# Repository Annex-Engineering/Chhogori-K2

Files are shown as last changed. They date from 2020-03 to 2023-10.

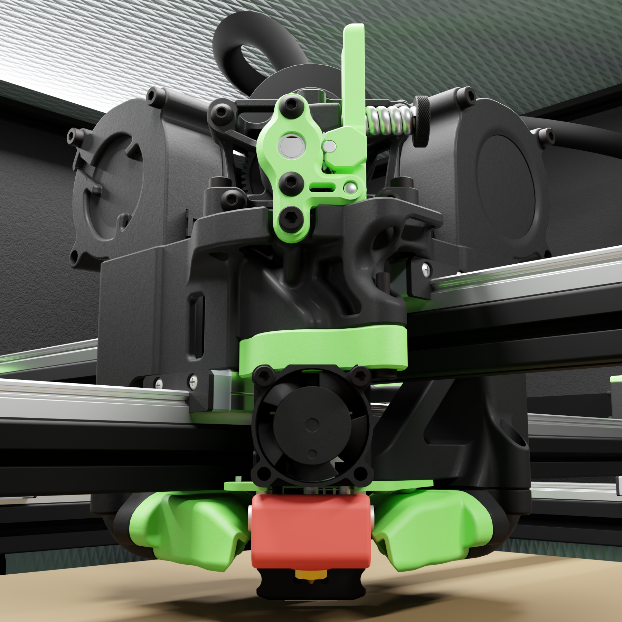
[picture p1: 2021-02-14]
Release_2_2/Images/1800px_k2_r2_render_toolhead_lower.png

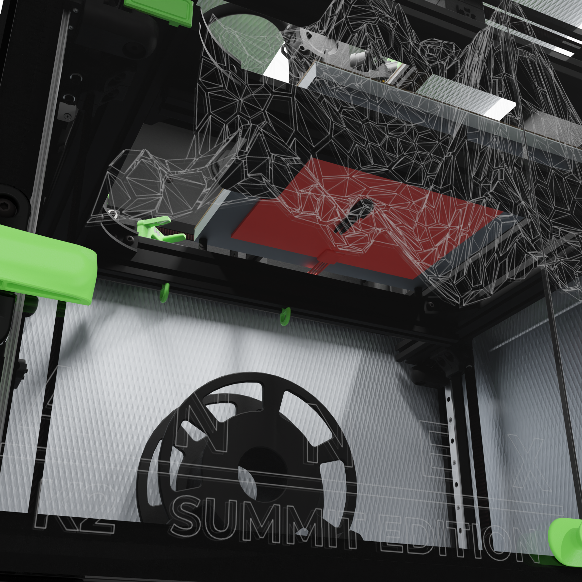
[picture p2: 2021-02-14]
Release_2_2/Images/1800px_k2_r2_render_lowertext.png

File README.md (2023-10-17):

# Chhogori (K2) Printer

## The Current Release is: Release 3 for XY Gantry and Release 2.2 for Z Drive

## Info:
Chhogori (K2): is a Medium Format, Direct Drive, Fully Enclosed FDM Printer.

This is an entirely scratch design, based on the efforts of the "Hypercube Overkill Project" for the XY Motion System, and inspired by all other prior repraps.

Our discord server can be found here: 

Join me on Discord (https://discord.gg/MzTR3zE)

BOM/Sourcing Guide for a 250x250x250 Build can be found here: https://docs.google.com/spreadsheets/d/1O3eyVuQ6M4F03MJSDs4Z71_XyNjXL5HFTZr1jsaAtRc/edit?usp=sharing

Frame Calculator: https://docs.google.com/spreadsheets/d/1hEwPB6xaeSEoHs37LAolL1LlHkrrIWt3NFW9NkrmP7g/edit?usp=sharing

## Stats:
- Fully Enclosed Design
- 2020 and 2040 Frame Members
- Insulated Build Chamber (Not Heated)
- Build Volumes of ~250^3 to 500^3 (use of whole plate available) + additional area to purge and wipe
     - Z can theoretically be 1m tall, just not fully supported or tested

- Direct Drive Extruder (Sherpa Mini or Ascender)

- Shortest Belt Paths Possible, 4 Motors, 2 Per X, 2 Per Y Axis
- Moving Bed, Fixed Gantry

- MGN12H Rails for XY Stationary Rails
- MGN15H Rails for XY Cross (Moving Members)
- MGN12C Rails for Z - using 2.2 parts
- Laser cut metal parts throughout for stiffness and strength (steel recommended in most places, aluminum on moving components)
- 12mm 2GT Belts on XY Motion 
- 12mm 2GT Belts with 20:1 Worm Drive on Z to lift the Bed 
	 - Hybrid Laser Cut Metal and Printed Part Construction
	 - Legacy Support for 15mm 3HTD belts also offered
- Heavy Duty Bearings
- NEMA17 Motors XYZ

- Minimal Printed Parts (ASA Required, PC Recommended for motion components)

- Fysetc Spider or S6 Controller + BTT Expander Board with Klipper Required
- Mosquito Style, Dragon Style, Mosquito Magnum+, Nitram's VolcoMosquito, and many other hotends supported
- 24V Power Standard, 48V Optional and Preferred
- Mains Bed

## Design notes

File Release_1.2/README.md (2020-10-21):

# Chhogori (K2) Printer - Summit Edition

These parts are purely pre-release at this point, please use with caution.

Use tab 2 on the frame calculator if you would like to build to this revision, please use discord for support

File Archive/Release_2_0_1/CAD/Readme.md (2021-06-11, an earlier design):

#CAD

Files are released in parasolid format only and will not be shared in any other format. (We have quality standards, STEP and IGES enjoy spitting out corrupted files, sorry)

By using these cad files, you agree to share any and all mods, that you develop, under the "ANNEX License", which can be found under the main level of this repo.

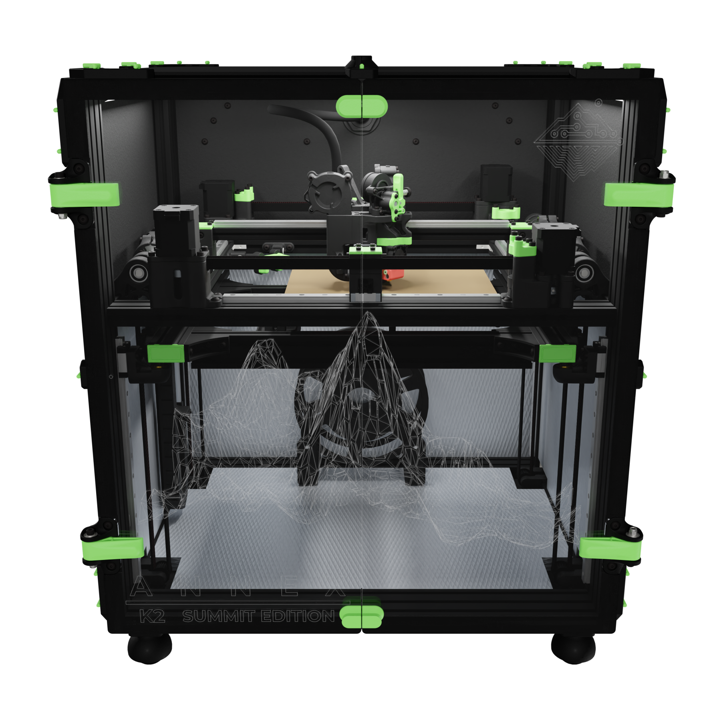
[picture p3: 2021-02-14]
Release_2_2/Images/1800px_k2_r2_render_center.png

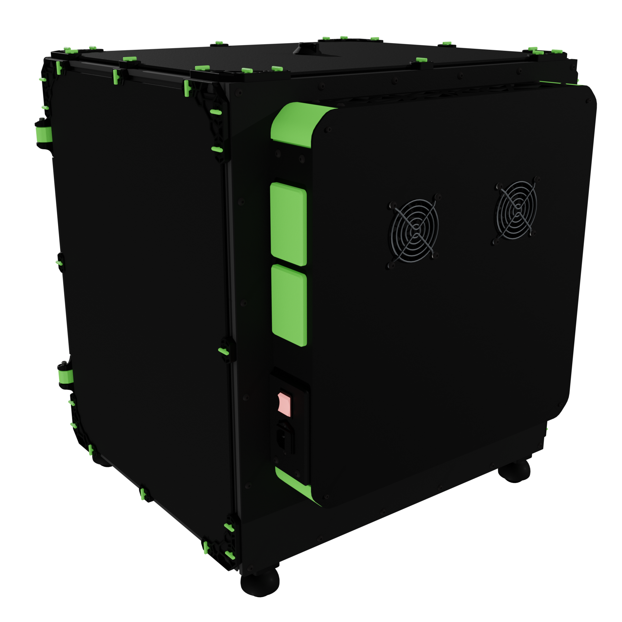
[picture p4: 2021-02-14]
Release_2_2/Images/1800px_k2_r2_render_rear.png

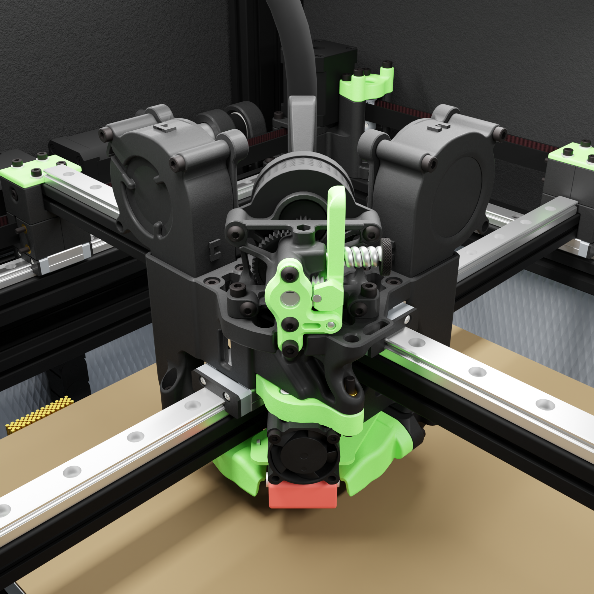
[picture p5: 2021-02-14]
Release_2_2/Images/1800px_k2_r2_render_toolhead_upper.png

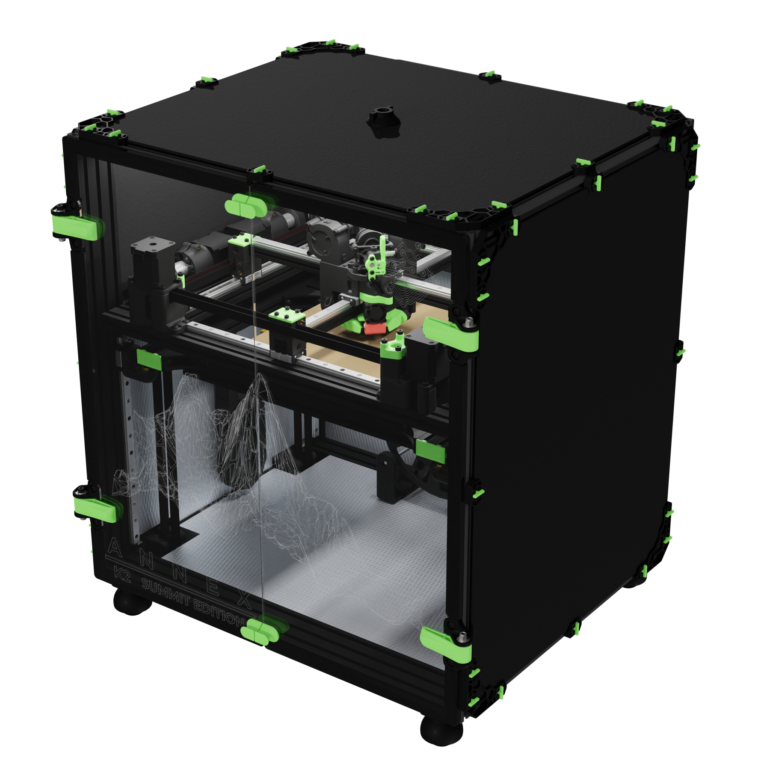
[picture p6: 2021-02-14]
Release_2_2/Images/1800px_k2_r2_render_dimetric.png

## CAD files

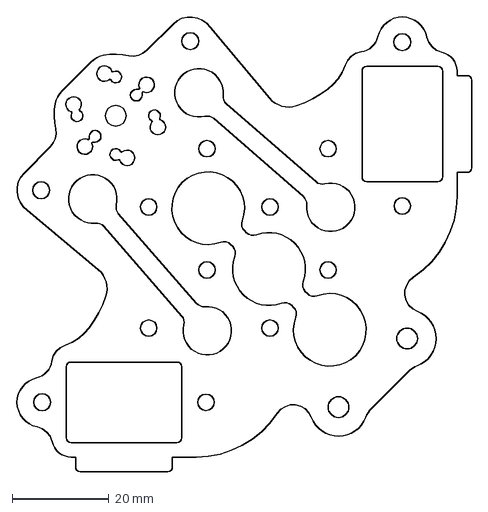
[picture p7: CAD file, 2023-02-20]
Release_3_0/DXFs/Toolhead/toolhead_main_plate_sherpa_mini_x2_rev4_2mm_aluminum.DXF
93.9 x 93.9 mm

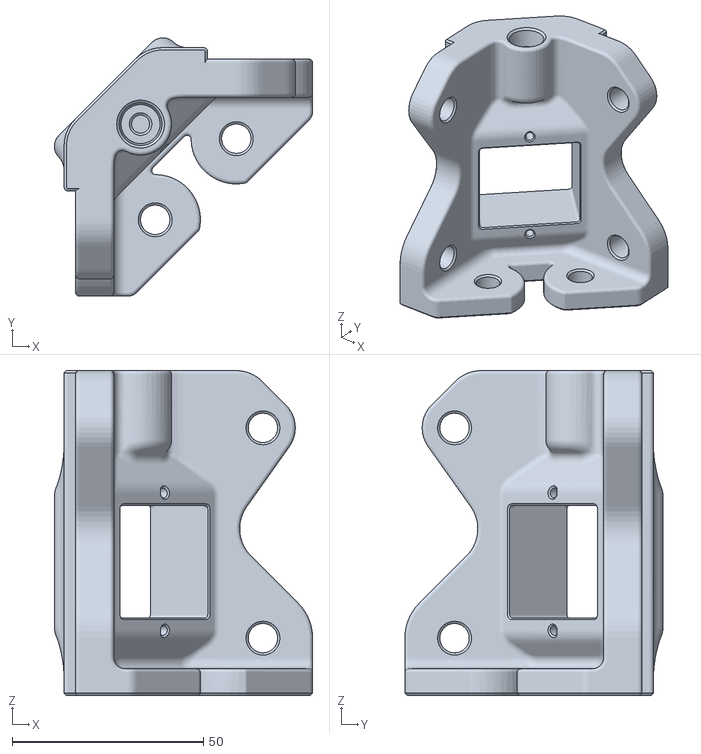
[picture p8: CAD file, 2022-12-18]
Release_3_0/STLs/Electronics_Box/electronics_box_corner_mains_inlet_x1_rev4.STL
67.6 x 67.6 x 85.0

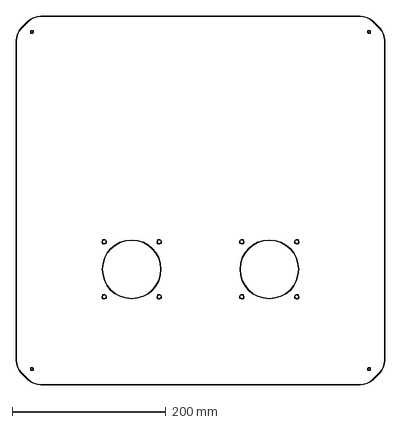
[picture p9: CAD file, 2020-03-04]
DXFs/Electronics_Box/electronics_box_cover_x1_rev1.DXF
479.0 x 479.0 mm

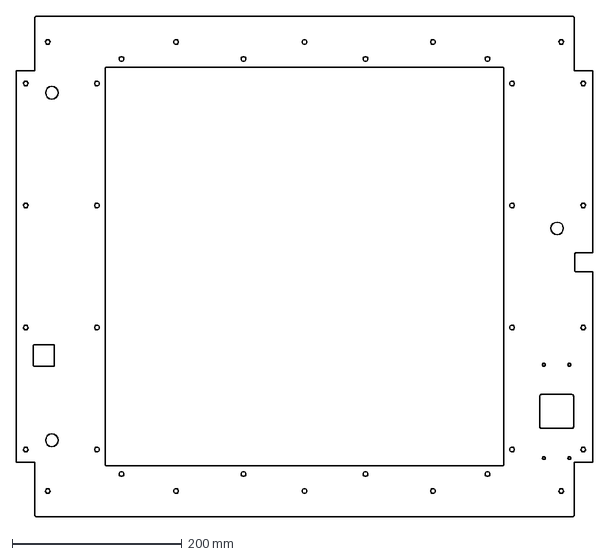
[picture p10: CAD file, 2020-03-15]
DXFs/Panels/Gantry_Deck_Panel_350mm_x_350mm_Rev3.DXF
680.0 x 590.0 mm

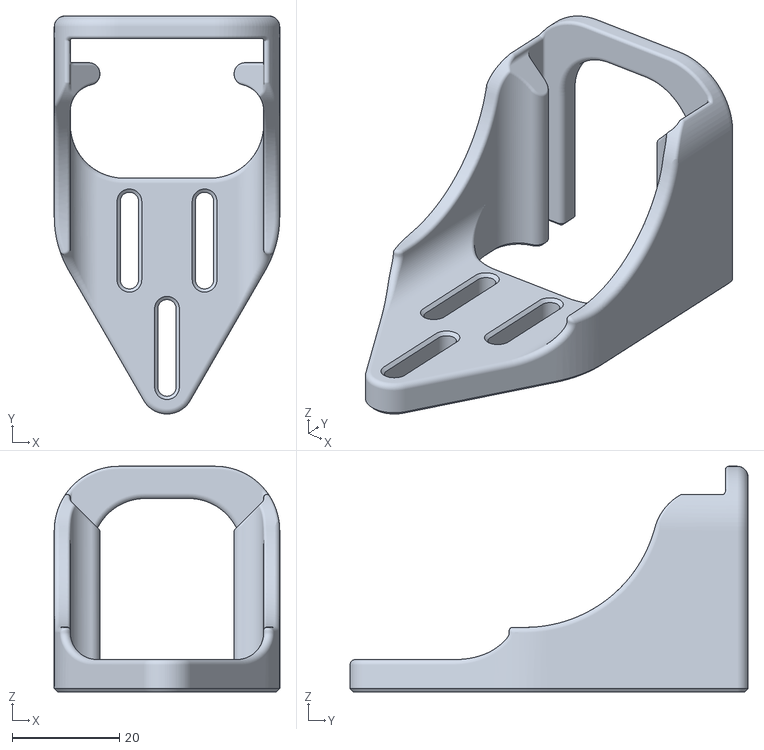
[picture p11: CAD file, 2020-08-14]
Release_1.2/STLs/Mesh_Bed_Probe/Magnetic_Probe/magnetic_probe_dock_x1_rev5.STL
42.0 x 74.1 x 42.0

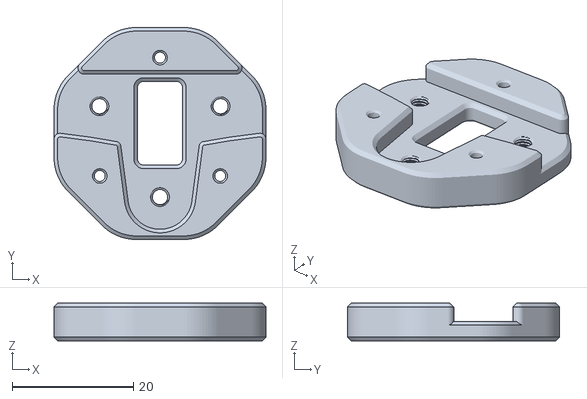
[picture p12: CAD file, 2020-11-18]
Release_1.2/STLs/Mesh_Bed_Probe/Piton_Probe/[a]_piton_probe_plate_6x3_x1_rev2.STL
35.0 x 35.0 x 6.20

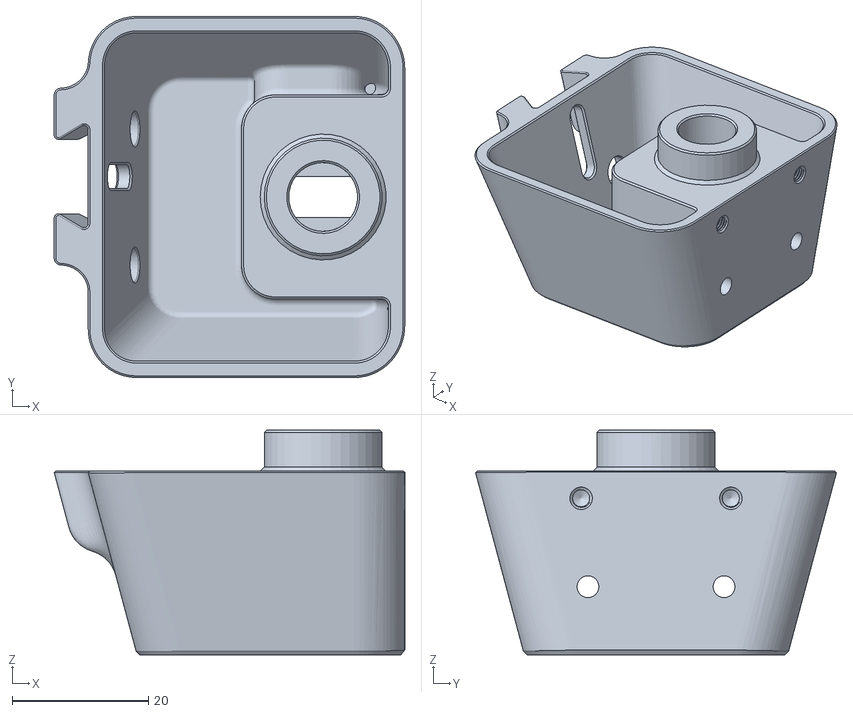
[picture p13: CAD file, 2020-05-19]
Release_1.2/STLs/Misc/z_endstop_housing_x1_rev1.STL
51.5 x 53.1 x 33.0

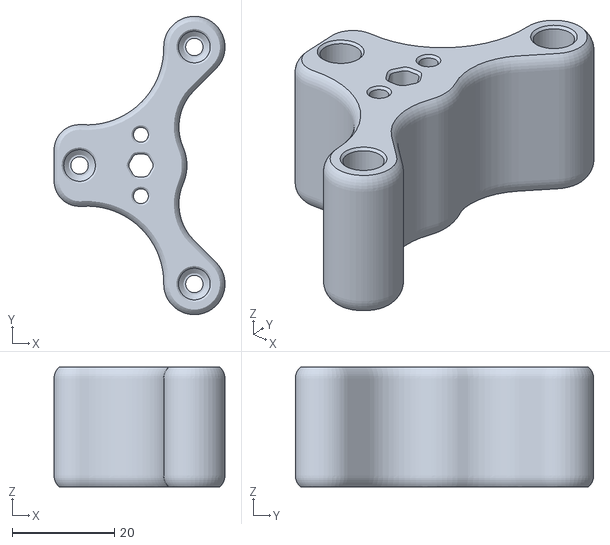
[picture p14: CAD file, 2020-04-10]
Release_1.2/STLs/XY_Carriage/Tool_Mounts/xy_carriage_mosquito_tool_mount_x1_rev3.STL
33.4 x 58.3 x 23.4

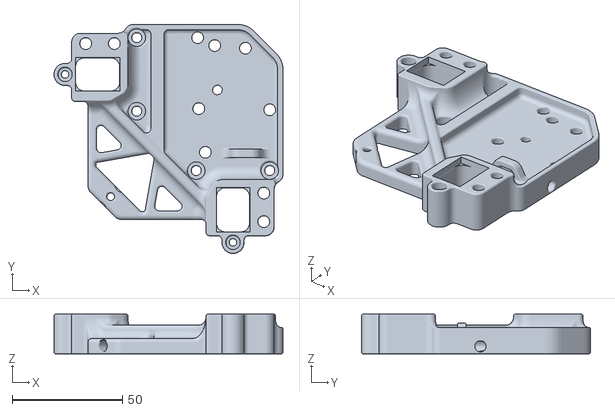
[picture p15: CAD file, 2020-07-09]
Release_1.2/STLs/XY_Carriage/Top_Plates/sherpa_tall_xy_carriage_top_plate_x1_rev1.STL
104.0 x 104.0 x 18.0

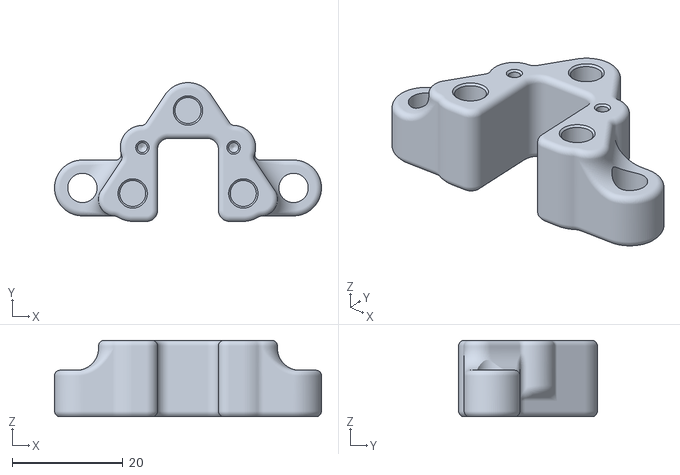
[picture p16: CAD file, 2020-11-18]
Release_1.2/STLs/XY_Carriage/xy_carriage_piton_probe_holder_mosquito_x1_rev3.STL
48.3 x 25.1 x 13.8

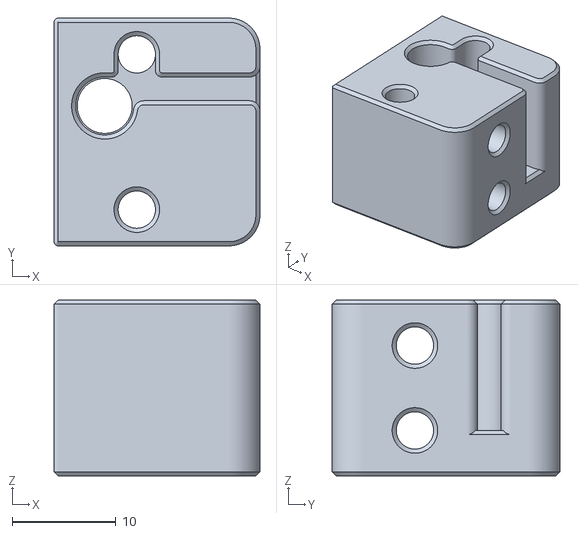
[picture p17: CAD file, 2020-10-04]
Release_1.2/STLs/XY_Gantry/xy_tensioner_left_20t_drive_x4_rev3.STL
19.9 x 22.0 x 17.0

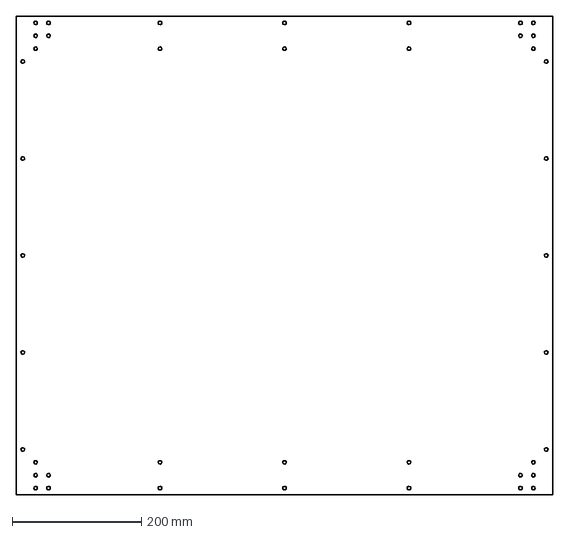
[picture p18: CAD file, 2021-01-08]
Release_2/DXFs/Optional_Laser_Cut_Panels/Bottom_500mm_x_500mm_Rev1.DXF
830.0 x 740.0 mm

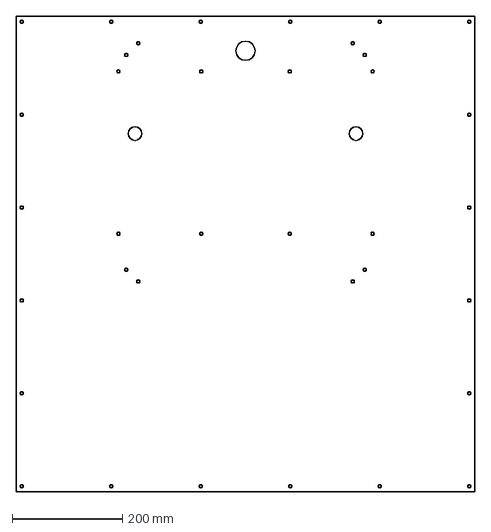
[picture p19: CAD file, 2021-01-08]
Release_2/DXFs/Panels/Back_Panel_500mm_x_500mm_Rev1.DXF
830.0 x 861.0 mm

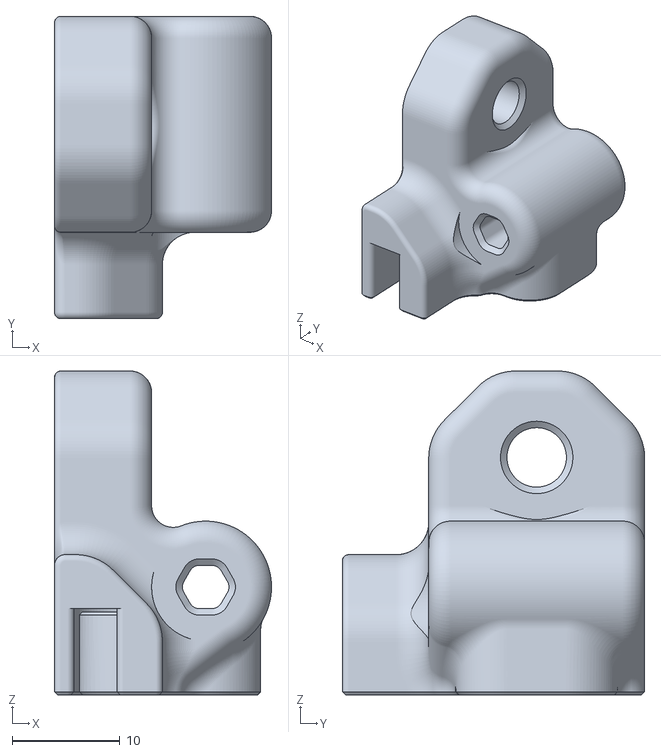
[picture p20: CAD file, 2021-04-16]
Release_2/STLs/Belted_Z_Drive/[a]_belted_z_tensioner_b1_x4_rev4.STL
20.1 x 28.0 x 30.0

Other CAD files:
Release_2/STLs/Electronics_Brackets/bigtreetech_skr_mounting_bracket_x2_rev4.STL
Release_2_1/DXFs/12mm_2GT_Belted_Z_Drive/3mm_stainless_belted_worm_z_metal_top_40+20to1_x4_rev1.DXF
Release_2_1/DXFs/15mm_3HTD_Belted_Z_Drive/3mm_stainless_belted_worm_z_metal_top_60to1_x4_rev2.DXF
Release_2_1/DXFs/Electronics_Box/electronics_box_side_panel_power_inet_x1_rev1.DXF
Archive/Release_1.2/CAD/BASS_Fan_Ducts.x_t
Archive/Release_1.2/CAD/FYSETC_S6_Mounting_Frame.x_t
Archive/Release_1.2/CAD/Front Door_Rev1.2-12-08-2020.x_t
Archive/Release_1.2/CAD/Piton_Probe_Assembly_11-18-2020.x_t
Archive/Release_1.2/DXFs/Electronics_Box/electronics_box_side_panel_TE_power_inlet_x1_rev2.DXF
Archive/Release_1.2/DXFs/Optional_Laser_Cut_Panels/Bottom_200mm_x_200mm_Rev1.DXF
Archive/Release_1.2/DXFs/Optional_Laser_Cut_Panels/Bottom_250mm_x_250mm_Rev1.DXF
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

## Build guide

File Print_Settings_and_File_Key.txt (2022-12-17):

Primary Color: nothing at start of file name
Accent Color: [a]_ at start of file name
Quantity Required: _x# near end of file name
File Revision: _Rev# at end of file name

Nozzle Size: 0.5mm 
Recommended FDM Materials: ASA, Polymaker or 3DXTech Recommended
Alternate Approved FDM Materials: PC, 3DXTech Recommended
Layer Height: 0.25mm
Extrusion Width: Forced 0.5mm
Infill Percentage: 40% minimum (at 0.8mm Width)
Infill Type: Grid, Gyroid, Honeycomb, Triangle or Cubic
Wall Count: 3 minimum (at 0.5mm Width)
Solid Top/Bottom Layers: 4 minimum (at 0.5mm Height)

Nozzle Size: 0.4mm 
Recommended FDM Materials: ASA, Polymaker or 3DXTech Recommended
Alternate Approved FDM Materials: PC, 3DXTech Recommended
Layer Height: 0.20mm or 0.25mm
Extrusion Width: Forced 0.4mm
Infill Percentage: 40% minimum (at 0.6mm Width)
Infill Type: Grid, Gyroid, Honeycomb, Triangle or Cubic
Wall Count: 4 minimum (at 0.4mm Width)
Solid Top/Bottom Layers: 4 minimum (at 0.25mm Height)

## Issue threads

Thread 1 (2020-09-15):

I don't understand what the endstop in this place does

du5778, 2020-09-15:
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

Tuz550, 2020-09-15:
The printer has a vertically moving bed, printing at the top and moving downwards. From the picture, it looks like that is the lowest extent of the Z axis.

Annex-Engineering, 2020-09-15:
Those switches are emergency stop buttons, because the bed is on springs, if one was to ram the nozzle into the bed by accident, this will turn the machine off. They are entirely optional.

Closed 2020-09-15.

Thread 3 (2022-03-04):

Assembly issues: 20:1 12mm worm Z drive

ameyp, 2022-03-04:
List of issues I encountered during assembly:

1. The long bolts holding the motor should be m3x45 instead of m3x40. The distance between the top and bottom of the drive is 39mm, leaving just 1mm on a 40mm bolt.
2. Some Aliexpress spur have 7mm hubs instead of 6mm, making it necessary to use multiple 1mm shims instead of 3mm spacers in order to get full tooth engagement between the worm and the spur

Closed 2024-04-24.

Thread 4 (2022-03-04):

Assembly issues: Z tensioner

ameyp, 2022-03-04:
List of issues I encountered during assembly:

- The two spacers that go on the shoulder bolt are swapped. The M5 one needs to be on the threaded side and the M6 one needs to be on the head side.

Closed 2024-04-24.

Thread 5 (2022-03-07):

Back right X stepper collides with right cable pass-through on the 2.2 frame setup

wlhlm, 2022-03-07:
Seems like back right stepper on the gantry obstructs the cable hole on the new 2040 frame:
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

Trails5000, 2022-03-07:
fixed with commit: https://github.com/Annex-Engineering/Chhogori-K2/commit/2baa07d4b91d5fae562b1b8711de88642b03c4b1

Closed 2022-03-07.

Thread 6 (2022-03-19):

Assembly issues: Z idler

ameyp, 2022-03-19:
List of issues I encountered during assembly:

- Tensioning the Z makes the rotation on which Z idlers are mounted rotate. The only ways to prevent this at present are by using external brackets or a bolted bottom panel

Closed 2024-04-24.

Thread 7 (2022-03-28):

Assembly issues: Backpack

ameyp, 2022-03-28:
List of issues I encountered during assembly

- The backpack extrusions should be mounted using M5x8 BHCS, the eDrawing says M5x10 BHCS. The latter are too long and bottom out with a 1mm gap left between the bolt head and the back panel
- The BOM needs a lot more M5x8 BHCS. Right now it says 2, but everything in the backpack uses them

Closed 2024-04-24.

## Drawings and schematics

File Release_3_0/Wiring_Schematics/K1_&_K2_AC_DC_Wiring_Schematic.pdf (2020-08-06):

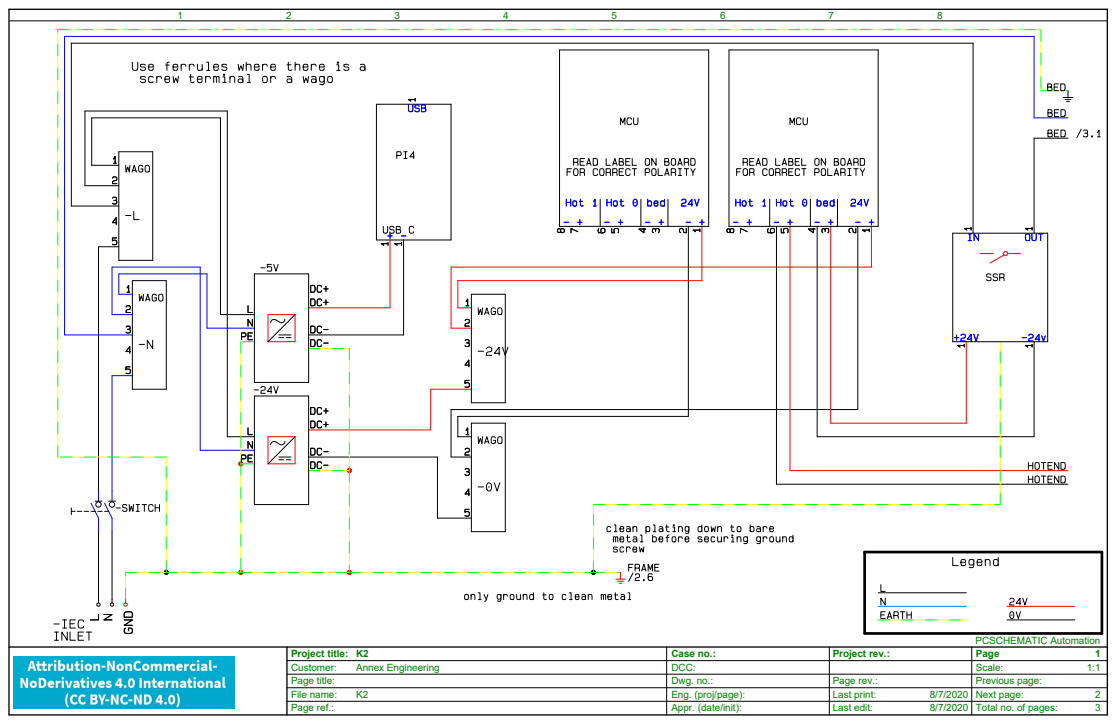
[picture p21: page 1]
PCSCHEMATIC Automation

Project title: K2 | Case no.: | Project rev.: | Page 1
Customer: Annex Engineering | DCC: | | Scale: 1:1
Page title: | Dwg. no.: | Page rev.: | Previous page:
File name: K2 | Eng. (proj/page): | Last print: 8/7/2020 | Next page: 2
Page ref.: | Appr. (date/init): | Last edit: 8/7/2020 | Total no. of pages: 3

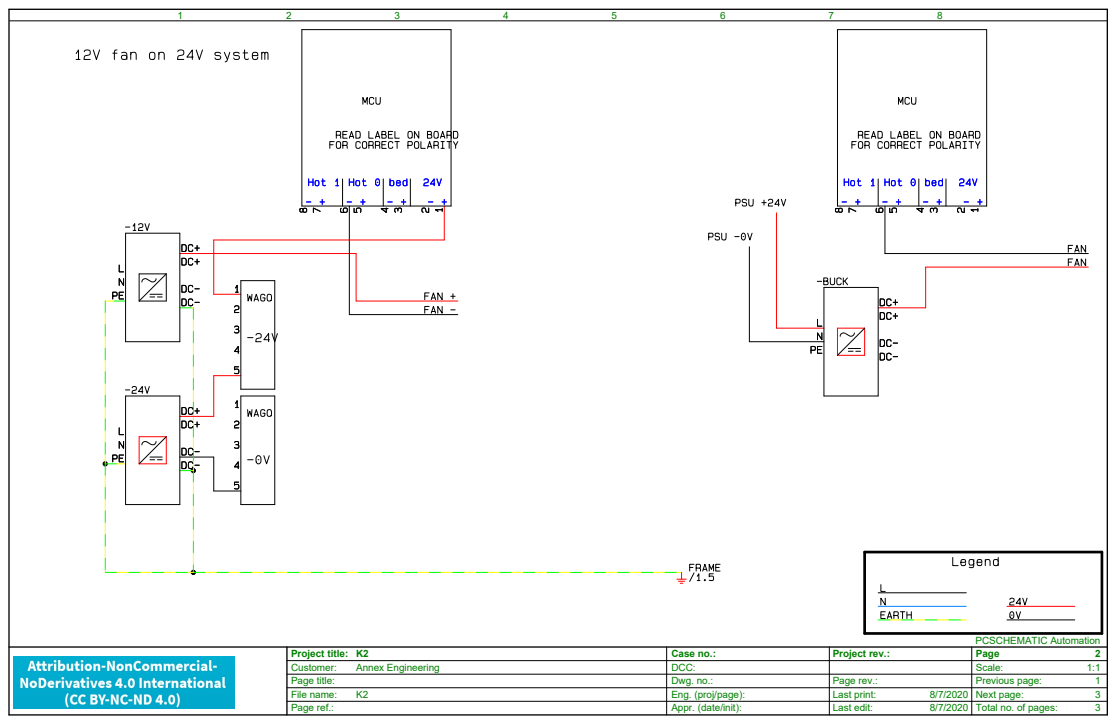
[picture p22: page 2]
PCSCHEMATIC Automation

Project title: K2 | Case no.: | Project rev.: | Page 2
Customer: Annex Engineering | DCC: | | Scale: 1:1

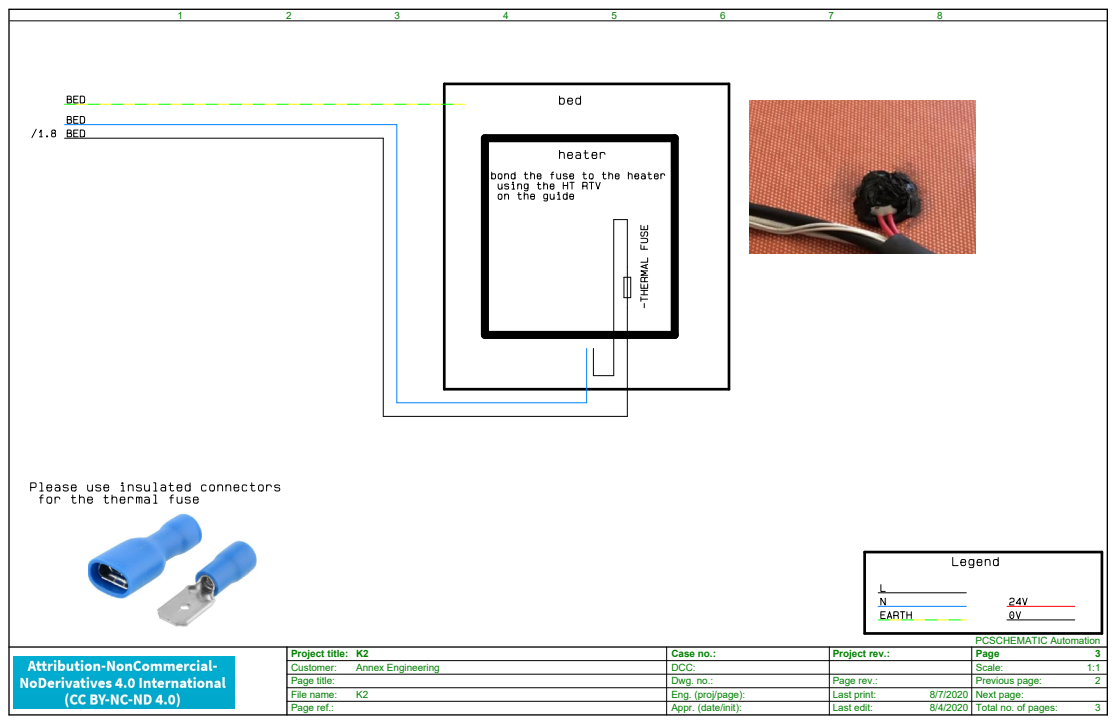
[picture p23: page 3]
PCSCHEMATIC Automation

Project title: K2 | Case no.: | Project rev.: | Page 3
Customer: Annex Engineering | DCC: | | Scale: 1:1

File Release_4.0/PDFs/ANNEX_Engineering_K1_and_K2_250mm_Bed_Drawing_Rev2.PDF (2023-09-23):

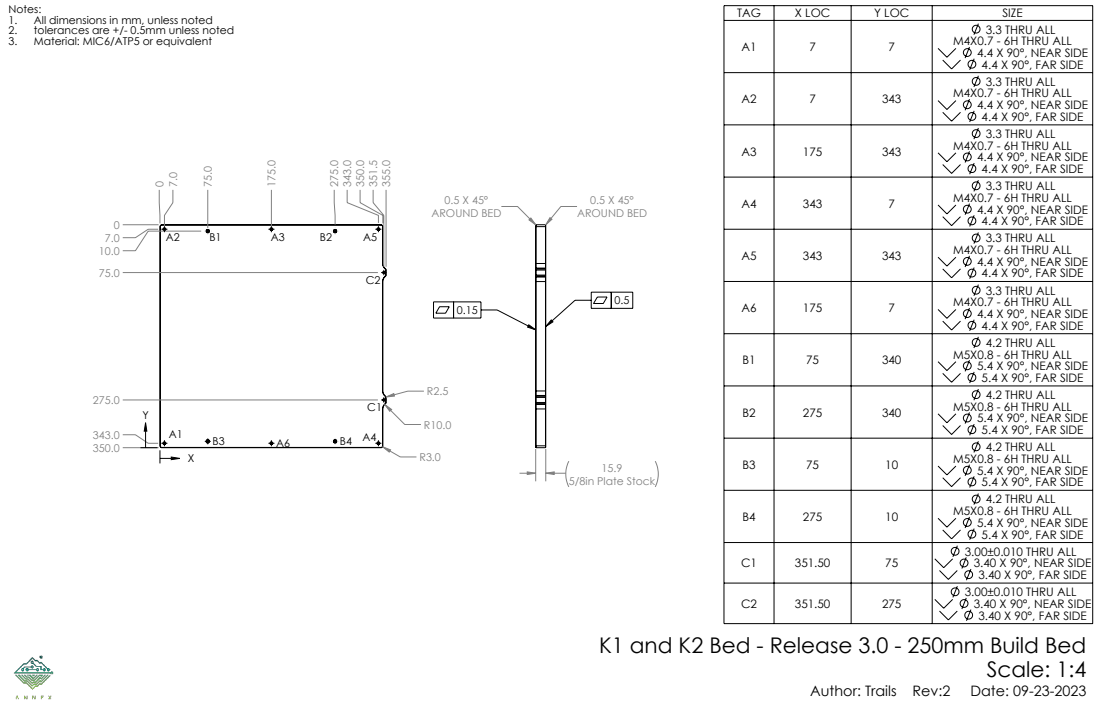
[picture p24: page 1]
5/8in Plate Stock; 0.5 X 45° AROUND BED; Scale: 1:4

Notes:
1. All dimensions in mm, unless noted
2. tolerances are +/- 0.5mm unless noted
3. Material: MIC6/ATP5 or equivalent

TAG | X LOC | Y LOC | SIZE
A1 | 7 | 7 | 3.3 THRU ALL M4X0.7 - 6H THRU ALL 4.4 X 90°, NEAR SIDE 4.4 X 90°, FAR SIDE

A2 | 7 | 343 | 3.3 THRU ALL M4X0.7 - 6H THRU ALL 4.4 X 90°, NEAR SIDE 4.4 X 90°, FAR SIDE

A3 | 175 | 343 | 3.3 THRU ALL M4X0.7 - 6H THRU ALL 4.4 X 90°, NEAR SIDE 4.4 X 90°, FAR SIDE

A4 | 343 | 7 | 3.3 THRU ALL M4X0.7 - 6H THRU ALL 4.4 X 90°, NEAR SIDE 4.4 X 90°, FAR SIDE

A5 | 343 | 343 | 3.3 THRU ALL M4X0.7 - 6H THRU ALL 4.4 X 90°, NEAR SIDE 4.4 X 90°, FAR SIDE

A6 | 175 | 7 | 3.3 THRU ALL M4X0.7 - 6H THRU ALL 4.4 X 90°, NEAR SIDE 4.4 X 90°, FAR SIDE

B1 | 75 | 340 | 4.2 THRU ALL M5X0.8 - 6H THRU ALL 5.4 X 90°, NEAR SIDE 5.4 X 90°, FAR SIDE

B2 | 275 | 340 | 4.2 THRU ALL M5X0.8 - 6H THRU ALL 5.4 X 90°, NEAR SIDE 5.4 X 90°, FAR SIDE

B3 | 75 | 10 | 4.2 THRU ALL M5X0.8 - 6H THRU ALL 5.4 X 90°, NEAR SIDE 5.4 X 90°, FAR SIDE

B4 | 275 | 10 | 4.2 THRU ALL M5X0.8 - 6H THRU ALL 5.4 X 90°, NEAR SIDE 5.4 X 90°, FAR SIDE

C1 | 351.50 | 75 | 3.00±0.010 THRU ALL 3.40 X 90°, NEAR SIDE 3.40 X 90°, FAR SIDE

C2 | 351.50 | 275 | 3.00±0.010 THRU ALL 3.40 X 90°, NEAR SIDE 3.40 X 90°, FAR SIDE

K1 and K2 Bed - Release 3.0 - 250mm Build Bed

Author: Trails Rev:2 Date: 09-23-2023

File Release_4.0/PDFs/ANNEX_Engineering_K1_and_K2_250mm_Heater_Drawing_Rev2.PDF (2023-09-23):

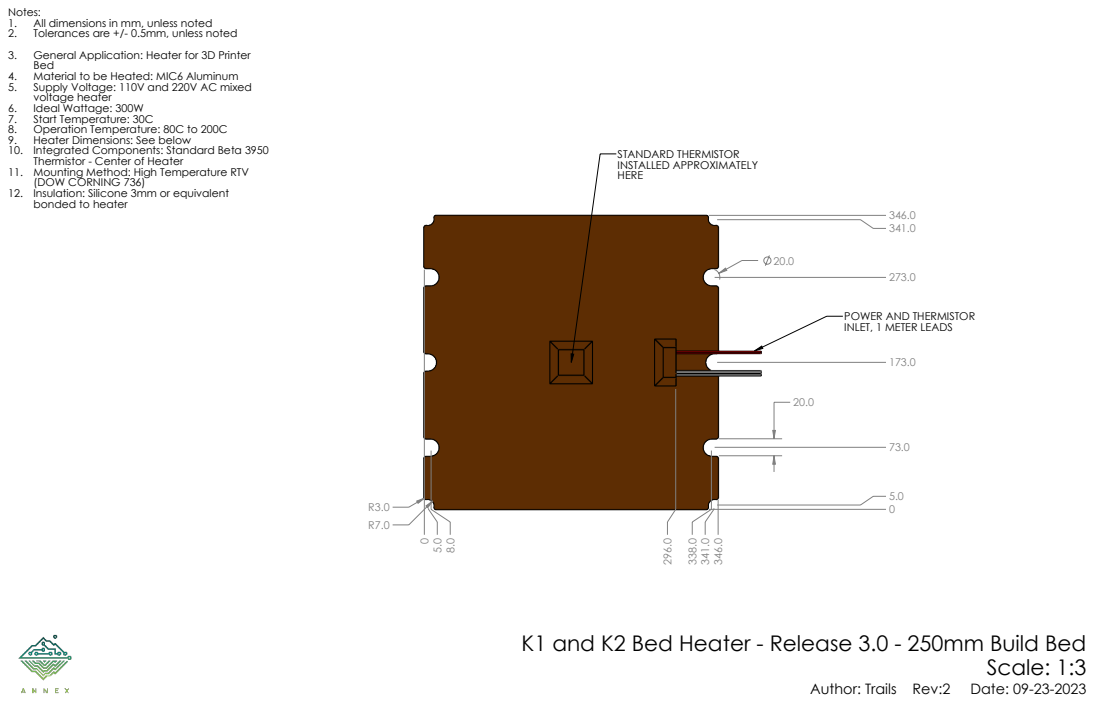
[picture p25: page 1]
STANDARD THERMISTOR INSTALLED APPROXIMATELY; Scale: 1:3

Notes:
1. All dimensions in mm, unless noted
2. Tolerances are +/- 0.5mm, unless noted
3. General Application: Heater for 3D Printer
Bed
4. Material to be Heated: MIC6 Aluminum
5. Supply Voltage: 110V and 220V AC mixed
voltage heater
6. Ideal Wattage: 300W
7. Start Temperature: 30C
8. Operation Temperature: 80C to 200C
9. Heater Dimensions: See below
10. Integrated Components: Standard Beta 3950
Thermistor - Center of Heater
11. Mounting Method: High Temperature RTV
(DOW CORNING 736)
12. Insulation: Silicone 3mm or equivalent
bonded to heater

POWER AND THERMISTOR
INLET, 1 METER LEADS

K1 and K2 Bed Heater - Release 3.0 - 250mm Build Bed

Author: Trails Rev:2 Date: 09-23-2023

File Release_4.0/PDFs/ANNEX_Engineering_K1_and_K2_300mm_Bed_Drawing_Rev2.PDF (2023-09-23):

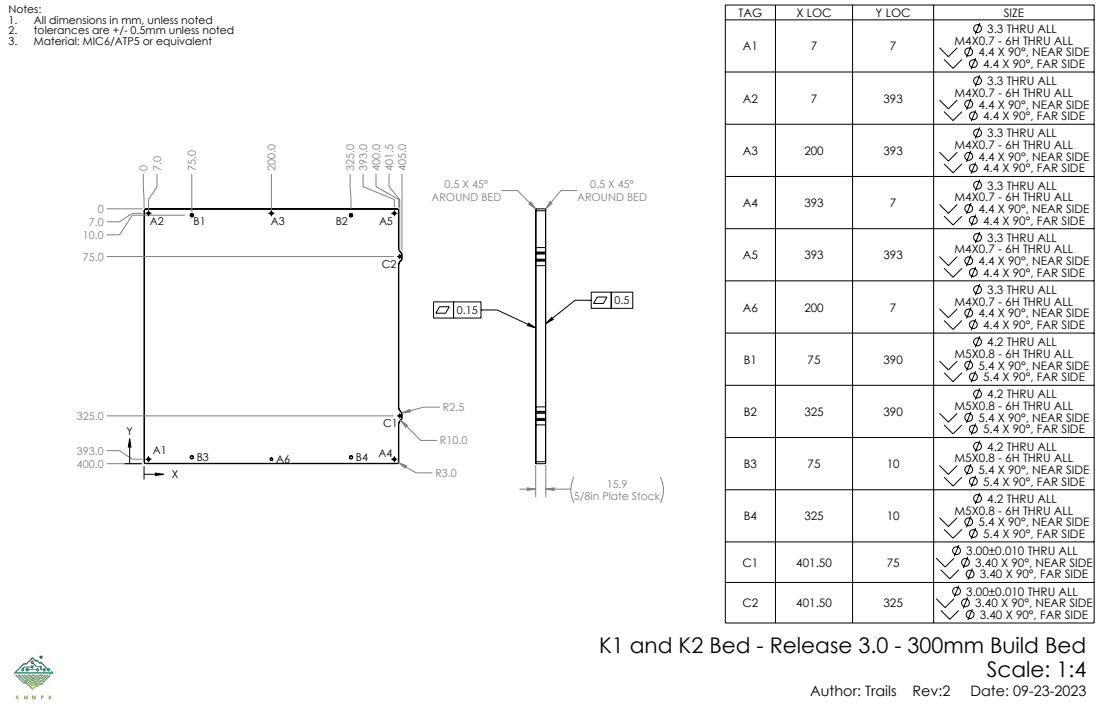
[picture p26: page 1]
5/8in Plate Stock; 0.5 X 45° AROUND BED; Scale: 1:4

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

A2 | 7 | 393 | 3.3 THRU ALL M4X0.7 - 6H THRU ALL 4.4 X 90°, NEAR SIDE 4.4 X 90°, FAR SIDE

A3 | 200 | 393 | 3.3 THRU ALL M4X0.7 - 6H THRU ALL 4.4 X 90°, NEAR SIDE 4.4 X 90°, FAR SIDE

A4 | 393 | 7 | 3.3 THRU ALL M4X0.7 - 6H THRU ALL 4.4 X 90°, NEAR SIDE 4.4 X 90°, FAR SIDE

A5 | 393 | 393 | 3.3 THRU ALL M4X0.7 - 6H THRU ALL 4.4 X 90°, NEAR SIDE 4.4 X 90°, FAR SIDE

A6 | 200 | 7 | 3.3 THRU ALL M4X0.7 - 6H THRU ALL 4.4 X 90°, NEAR SIDE 4.4 X 90°, FAR SIDE

B1 | 75 | 390 | 4.2 THRU ALL M5X0.8 - 6H THRU ALL 5.4 X 90°, NEAR SIDE 5.4 X 90°, FAR SIDE

B2 | 325 | 390 | 4.2 THRU ALL M5X0.8 - 6H THRU ALL 5.4 X 90°, NEAR SIDE 5.4 X 90°, FAR SIDE

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

B4 | 325 | 10 | 4.2 THRU ALL M5X0.8 - 6H THRU ALL 5.4 X 90°, NEAR SIDE 5.4 X 90°, FAR SIDE

C1 | 401.50 | 75 | 3.00±0.010 THRU ALL 3.40 X 90°, NEAR SIDE 3.40 X 90°, FAR SIDE

C2 | 401.50 | 325 | 3.00±0.010 THRU ALL 3.40 X 90°, NEAR SIDE 3.40 X 90°, FAR SIDE

K1 and K2 Bed - Release 3.0 - 300mm Build Bed

Author: Trails Rev:2 Date: 09-23-2023

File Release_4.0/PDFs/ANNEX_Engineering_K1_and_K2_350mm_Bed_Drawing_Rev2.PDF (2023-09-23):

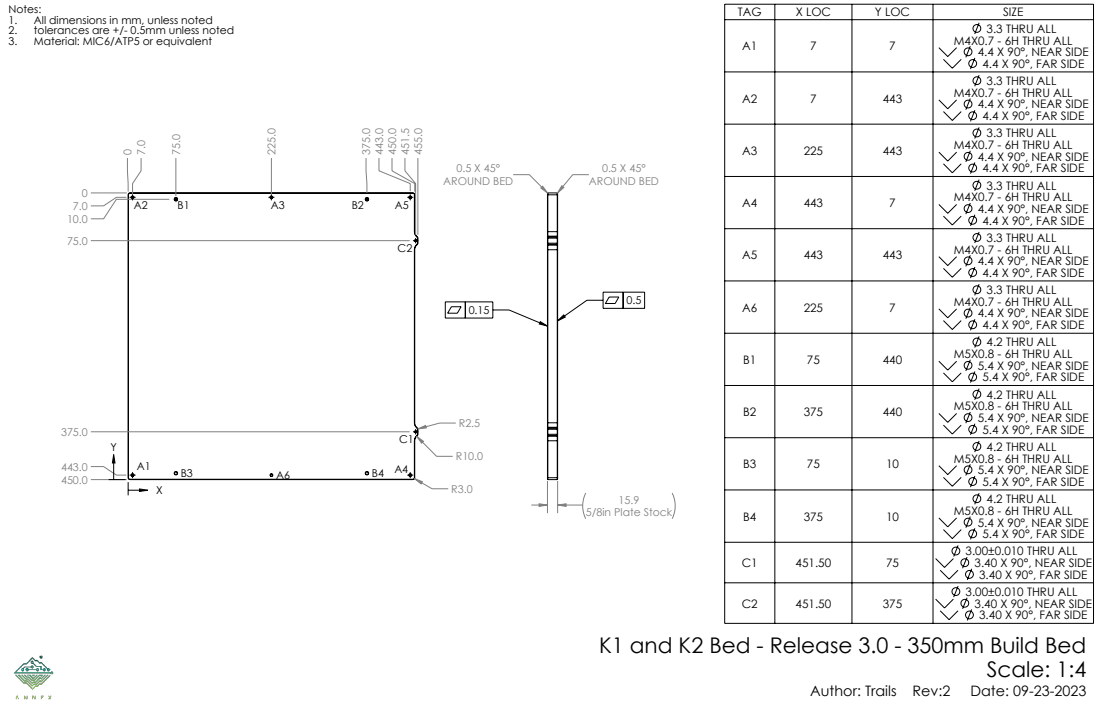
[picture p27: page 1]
5/8in Plate Stock; 0.5 X 45° AROUND BED; Scale: 1:4

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

A2 | 7 | 443 | 3.3 THRU ALL M4X0.7 - 6H THRU ALL 4.4 X 90°, NEAR SIDE 4.4 X 90°, FAR SIDE

A3 | 225 | 443 | 3.3 THRU ALL M4X0.7 - 6H THRU ALL 4.4 X 90°, NEAR SIDE 4.4 X 90°, FAR SIDE

A4 | 443 | 7 | 3.3 THRU ALL M4X0.7 - 6H THRU ALL 4.4 X 90°, NEAR SIDE 4.4 X 90°, FAR SIDE

A5 | 443 | 443 | 3.3 THRU ALL M4X0.7 - 6H THRU ALL 4.4 X 90°, NEAR SIDE 4.4 X 90°, FAR SIDE

A6 | 225 | 7 | 3.3 THRU ALL M4X0.7 - 6H THRU ALL 4.4 X 90°, NEAR SIDE 4.4 X 90°, FAR SIDE

B1 | 75 | 440 | 4.2 THRU ALL M5X0.8 - 6H THRU ALL 5.4 X 90°, NEAR SIDE 5.4 X 90°, FAR SIDE

B2 | 375 | 440 | 4.2 THRU ALL M5X0.8 - 6H THRU ALL 5.4 X 90°, NEAR SIDE 5.4 X 90°, FAR SIDE

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

B4 | 375 | 10 | 4.2 THRU ALL M5X0.8 - 6H THRU ALL 5.4 X 90°, NEAR SIDE 5.4 X 90°, FAR SIDE

C1 | 451.50 | 75 | 3.00±0.010 THRU ALL 3.40 X 90°, NEAR SIDE 3.40 X 90°, FAR SIDE

C2 | 451.50 | 375 | 3.00±0.010 THRU ALL 3.40 X 90°, NEAR SIDE 3.40 X 90°, FAR SIDE

K1 and K2 Bed - Release 3.0 - 350mm Build Bed

Author: Trails Rev:2 Date: 09-23-2023

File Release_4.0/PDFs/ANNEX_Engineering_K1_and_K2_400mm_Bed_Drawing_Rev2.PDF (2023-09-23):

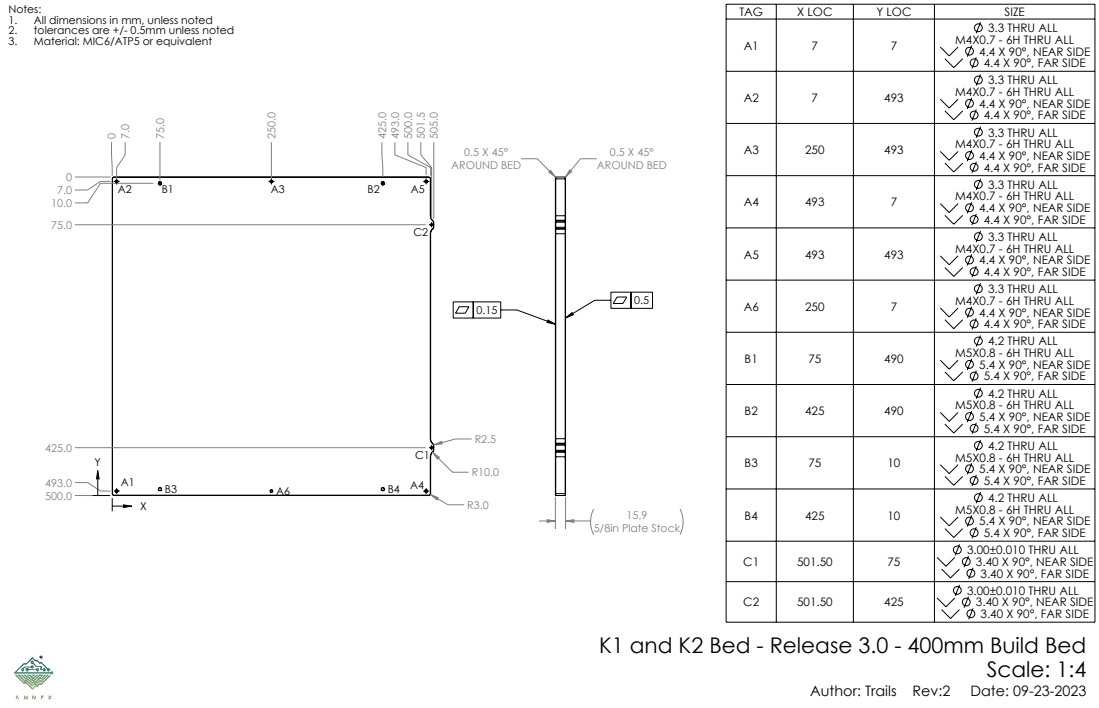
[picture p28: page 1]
5/8in Plate Stock; 0.5 X 45° AROUND BED; Scale: 1:4

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

A2 | 7 | 493 | 3.3 THRU ALL M4X0.7 - 6H THRU ALL 4.4 X 90°, NEAR SIDE 4.4 X 90°, FAR SIDE

A3 | 250 | 493 | 3.3 THRU ALL M4X0.7 - 6H THRU ALL 4.4 X 90°, NEAR SIDE 4.4 X 90°, FAR SIDE

A4 | 493 | 7 | 3.3 THRU ALL M4X0.7 - 6H THRU ALL 4.4 X 90°, NEAR SIDE 4.4 X 90°, FAR SIDE

A5 | 493 | 493 | 3.3 THRU ALL M4X0.7 - 6H THRU ALL 4.4 X 90°, NEAR SIDE 4.4 X 90°, FAR SIDE

A6 | 250 | 7 | 3.3 THRU ALL M4X0.7 - 6H THRU ALL 4.4 X 90°, NEAR SIDE 4.4 X 90°, FAR SIDE

B1 | 75 | 490 | 4.2 THRU ALL M5X0.8 - 6H THRU ALL 5.4 X 90°, NEAR SIDE 5.4 X 90°, FAR SIDE

B2 | 425 | 490 | 4.2 THRU ALL M5X0.8 - 6H THRU ALL 5.4 X 90°, NEAR SIDE 5.4 X 90°, FAR SIDE

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

B4 | 425 | 10 | 4.2 THRU ALL M5X0.8 - 6H THRU ALL 5.4 X 90°, NEAR SIDE 5.4 X 90°, FAR SIDE

C1 | 501.50 | 75 | 3.00±0.010 THRU ALL 3.40 X 90°, NEAR SIDE 3.40 X 90°, FAR SIDE

C2 | 501.50 | 425 | 3.00±0.010 THRU ALL 3.40 X 90°, NEAR SIDE 3.40 X 90°, FAR SIDE

K1 and K2 Bed - Release 3.0 - 400mm Build Bed

Author: Trails Rev:2 Date: 09-23-2023

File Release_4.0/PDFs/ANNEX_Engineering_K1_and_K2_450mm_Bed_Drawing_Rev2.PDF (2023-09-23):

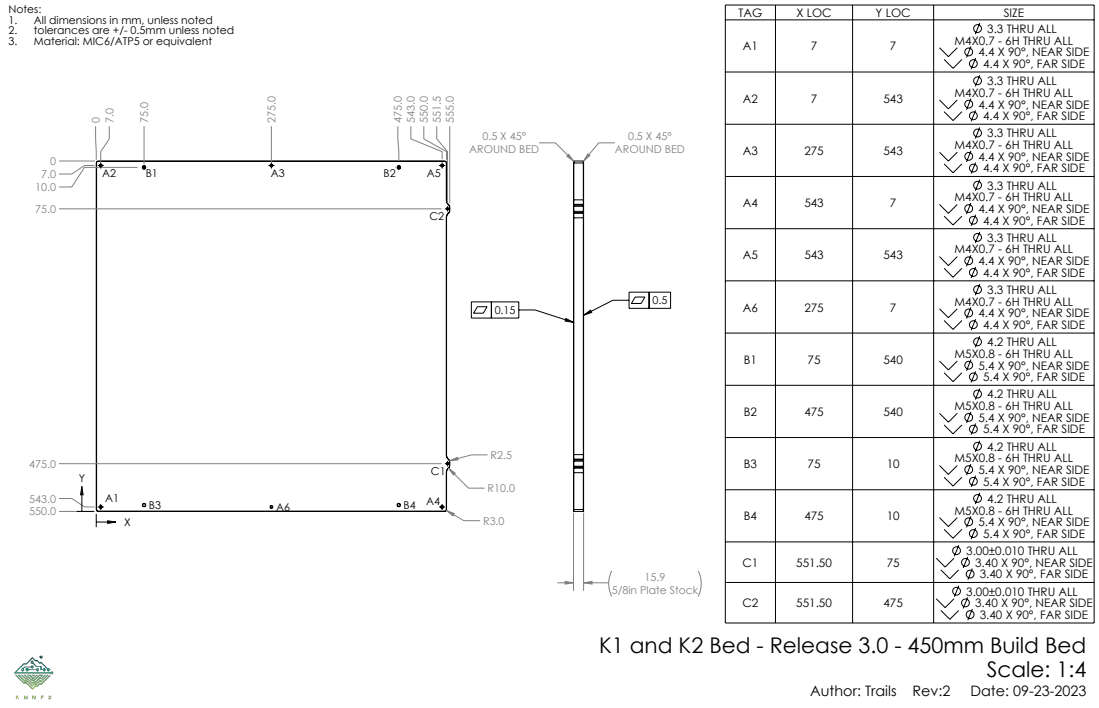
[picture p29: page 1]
0.5 X 45° AROUND BED; Scale: 1:4

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

A2 | 7 | 543 | 3.3 THRU ALL M4X0.7 - 6H THRU ALL 4.4 X 90°, NEAR SIDE 4.4 X 90°, FAR SIDE

A3 | 275 | 543 | 3.3 THRU ALL M4X0.7 - 6H THRU ALL 4.4 X 90°, NEAR SIDE 4.4 X 90°, FAR SIDE

A4 | 543 | 7 | 3.3 THRU ALL M4X0.7 - 6H THRU ALL 4.4 X 90°, NEAR SIDE 4.4 X 90°, FAR SIDE

A5 | 543 | 543 | 3.3 THRU ALL M4X0.7 - 6H THRU ALL 4.4 X 90°, NEAR SIDE 4.4 X 90°, FAR SIDE

A6 | 275 | 7 | 3.3 THRU ALL M4X0.7 - 6H THRU ALL 4.4 X 90°, NEAR SIDE 4.4 X 90°, FAR SIDE

B1 | 75 | 540 | 4.2 THRU ALL M5X0.8 - 6H THRU ALL 5.4 X 90°, NEAR SIDE 5.4 X 90°, FAR SIDE

B2 | 475 | 540 | 4.2 THRU ALL M5X0.8 - 6H THRU ALL 5.4 X 90°, NEAR SIDE 5.4 X 90°, FAR SIDE

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

B4 | 475 | 10 | 4.2 THRU ALL M5X0.8 - 6H THRU ALL 5.4 X 90°, NEAR SIDE 5.4 X 90°, FAR SIDE

C1 | 551.50 | 75 | 3.00±0.010 THRU ALL 3.40 X 90°, NEAR SIDE 3.40 X 90°, FAR SIDE

5/8in Plate Stock
K1 and K2 Bed - Release 3.0 - 450mm Build Bed

C2 | 551.50 | 475 | 3.00±0.010 THRU ALL 3.40 X 90°, NEAR SIDE 3.40 X 90°, FAR SIDE

Author: Trails Rev:2 Date: 09-23-2023

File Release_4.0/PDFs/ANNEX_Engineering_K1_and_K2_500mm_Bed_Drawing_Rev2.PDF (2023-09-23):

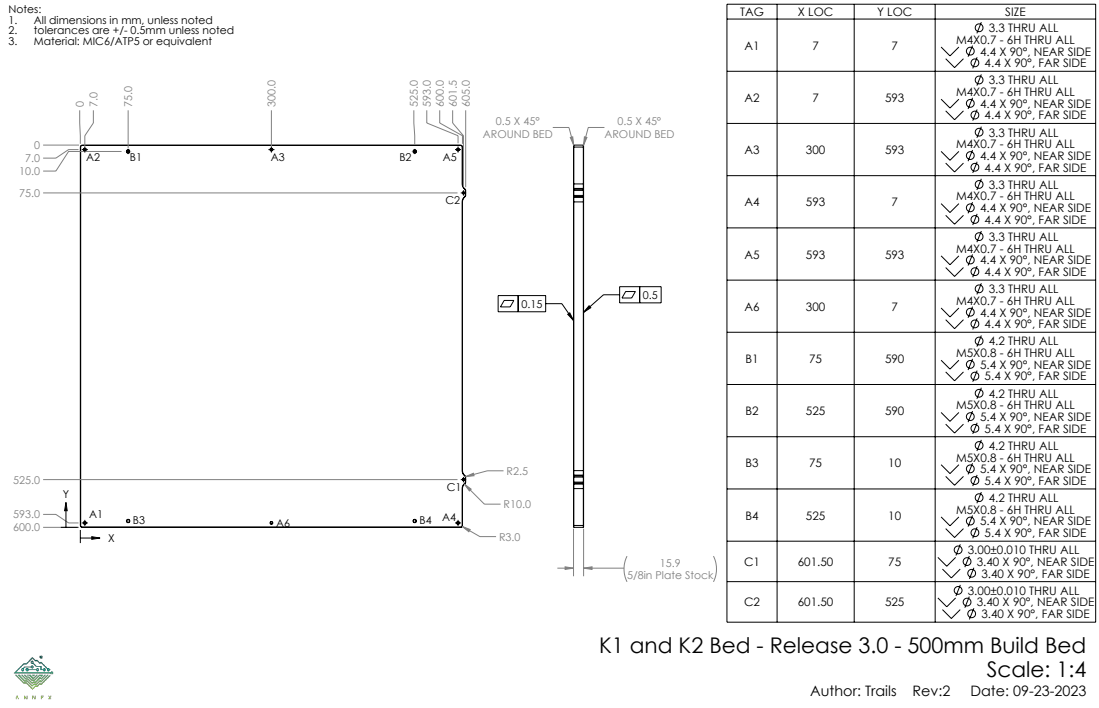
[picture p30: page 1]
5/8in Plate Stock; 0.5 X 45° AROUND BED; Scale: 1:4

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

A2 | 7 | 593 | 3.3 THRU ALL M4X0.7 - 6H THRU ALL 4.4 X 90°, NEAR SIDE 4.4 X 90°, FAR SIDE

A3 | 300 | 593 | 3.3 THRU ALL M4X0.7 - 6H THRU ALL 4.4 X 90°, NEAR SIDE 4.4 X 90°, FAR SIDE

A4 | 593 | 7 | 3.3 THRU ALL M4X0.7 - 6H THRU ALL 4.4 X 90°, NEAR SIDE 4.4 X 90°, FAR SIDE

A5 | 593 | 593 | 3.3 THRU ALL M4X0.7 - 6H THRU ALL 4.4 X 90°, NEAR SIDE 4.4 X 90°, FAR SIDE

A6 | 300 | 7 | 3.3 THRU ALL M4X0.7 - 6H THRU ALL 4.4 X 90°, NEAR SIDE 4.4 X 90°, FAR SIDE

B1 | 75 | 590 | 4.2 THRU ALL M5X0.8 - 6H THRU ALL 5.4 X 90°, NEAR SIDE 5.4 X 90°, FAR SIDE

B2 | 525 | 590 | 4.2 THRU ALL M5X0.8 - 6H THRU ALL 5.4 X 90°, NEAR SIDE 5.4 X 90°, FAR SIDE

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

B4 | 525 | 10 | 4.2 THRU ALL M5X0.8 - 6H THRU ALL 5.4 X 90°, NEAR SIDE 5.4 X 90°, FAR SIDE

C1 | 601.50 | 75 | 3.00±0.010 THRU ALL 3.40 X 90°, NEAR SIDE 3.40 X 90°, FAR SIDE

C2 | 601.50 | 525 | 3.00±0.010 THRU ALL 3.40 X 90°, NEAR SIDE 3.40 X 90°, FAR SIDE

K1 and K2 Bed - Release 3.0 - 500mm Build Bed

Author: Trails Rev:2 Date: 09-23-2023

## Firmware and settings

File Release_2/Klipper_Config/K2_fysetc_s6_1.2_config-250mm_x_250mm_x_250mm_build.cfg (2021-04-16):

# This file has been created by Feb, of Annex Engineering, for the K2 3D Printer.
# Please change settings for your specific build or ensure you place your items in the same spots on the same MCU as I have.
# I've added as many options as I can think of for different displays as well as listed the available commands you can use via the terminal at the bottom of this configuration file.

# This is for a dockable z probe only, do not attempt to use this on a fixed z probe printer

#THIS CONFIG IS FOR A 250mm x 250mm x 250mm K1 PRINTER ONLY FOR THE FYSETC S6 1.2 CONTROLLER
#PLEASE READ THE WHOLE CONFIG BEFORE ATTEMPTING TO DO ANYTHING
#CONNECTORS/PORTS ON THE CONTROLLERS ARE NOTED WITH COMMENTS FOR EACH LOCATION/INPUT/OUTPUT

#How do I upgrade to the latest software?
#The general way to upgrade is to ssh into the Raspberry Pi and run:
#cd ~/klipper
#git pull
#~/klipper/scripts/install-octopi.sh

# Then one can recompile and flash the micro-controller code. For example:
#make menuconfig
#make clean
#make
#sudo service klipper stop
#make flash FLASH_DEVICE=vid:pid (where "vid:pid" is the device ID found using "lsusb")
#sudo service klipper start

# Obtaining your USB ID to flash with:
# disconnect all of the boards except the one you would like to flash
# type the "lsusb" command into the terminal
# note the USB ID (ex: "1d50:614e", vid and pid are each a 4 digit hex string)
# use the command above "make flash ...."

# This file contains common pin mappings for the Fysetc S6 board, version 1.2.
# To use this config, the firmware should be compiled for the STM32F446.
# When calling "menuconfig", enable "extra low-level configuration setup"
# and select the "12MHz crystal" as clock reference
# For flashing, write the compiled klipper.bin to memory location 0x08000000
# This address is applied automatically when you flash the board ^^^

#However, it's often the case that only the host software changes. In this case, one can update and restart just the host software with:
#cd ~/klipper
#git pull
#sudo service klipper restart
#If after using this shortcut the software warns about needing to reflash the micro-controller or some other unusual error occurs, then follow the full upgrade steps outlined above. Note that the RESTART and FIRMWARE_RESTART g-code commands do not load new software - the above "sudo service klipper restart" and "make flash" commands are needed for a software change to take effect.

# use the following modifiers before the pin definition (ex: ^!ar99)
# ! 			invert the logic
# ^ 			activate 5v pullup (does not apply to all pins)
# mcu_name: 	use pins on additional MCU (ex: z:ar10)


# MCU S6 #1
[mcu] 
	#You will need to set this definition manually following the instructions in the line below
#	obtain definition by "ls -l /dev/serial/by-id/" then unplug to verify
serial: /dev/serial/by-id/usb-Klipper_Klipper_firmware_12345-if00
restart_method: command

# MCU S6 #2
[mcu s62] 
#	You will need to set this definition manually following the instructions in the line below
#	obtain definition by "ls -l /dev/serial/by-id/" then unplug to verify
serial: /dev/serial/by-id/usb-Klipper_Klipper_firmware_12345-if00
restart_method: command


#Printer Speeds and Accels
[printer]
kinematics: cartesian
max_velocity: 500
max_accel: 2000 #change this to 7500 after commissioning
max_z_velocity: 8
max_z_accel: 5
square_corner_velocity: 5.0

#Gcode G2/G3 Arc Support
[gcode_arcs]
resolution: 0.1

#Input Shaper Settings
# you need to tune your printer for this, if your lazy you can use these values as a starting point
# [input_shaper]
# shaper_freq_x: 59 #(100*8)/13.5
# shaper_freq_y: 51 #(100*8)/15.75
# shaper_type: mzv


# Stepper Configs
[stepper_x]
# connected to X Stepper on S6 #1
step_pin: PE11
dir_pin: PE10
enable_pin: !PE12
# 20t Pulley, 2mm Pitch on a 0.9deg Motor
rotation_distance: 40
microsteps: 16
full_steps_per_rotation: 400
# connected to virtual endstop
endstop_pin: tmc2209_stepper_x:virtual_endstop 
position_min: 0
position_endstop: 260
position_max: 260
homing_speed: 50.0
homing_positive_dir: true

[stepper_x1]
# connected to Y Stepper on S6 #1
step_pin: PD8
dir_pin: !PB12
enable_pin: !PD9
# 20t Pulley, 2mm Pitch on a 0.9deg Motor
rotation_distance: 40
microsteps: 16
full_steps_per_rotation: 400
# connected to virtual endstop
endstop_pin: tmc2209_stepper_x1:virtual_endstop 



[stepper_y]
# connected to E0 Stepper on S6 #1
step_pin: PD5
dir_pin: PD6
enable_pin: !PD4
# 20t Pulley, 2mm Pitch on a 0.9deg Motor
rotation_distance: 40
microsteps: 16
full_steps_per_rotation: 400
# connected to virtual endstop
endstop_pin: tmc2209_stepper_y:virtual_endstop 
position_min: 0
position_endstop: 260
position_max: 260
homing_speed: 50.0
homing_positive_dir: true

[stepper_y1]
# connected to E1 Stepper on S6 #1
step_pin: PE6
dir_pin: !PC13
enable_pin: !PE5
# 20t Pulley, 2mm Pitch on a 0.9deg Motor
rotation_distance: 40
microsteps: 16
full_steps_per_rotation: 400
# connected to virtual endstop
endstop_pin: tmc2209_stepper_y1:virtual_endstop 



[stepper_z]
# connected to X Stepper on S6 #2 (Front Left Stepper, from top)
step_pin: s62:PE11
dir_pin: !s62:PE10
enable_pin: !s62:PE12
# Z Axis Steps per mm, uncomment out the step distance line for which motor/drive setup you are using
# SFU1204 Ballscrew attached to a 1.8 deg Motor
#rotation_distance: 16
#microsteps: 4
#full_steps_per_rotation: 200

# 20t Pulley, 3mm Pitch on a 1.8deg Motor with a 13.7:1 gearbox attached
#rotation_distance: 60
#microsteps: 4
#full_steps_per_rotation: 200
#gear_ratio: 137:10

# 20t Pulley, 3mm Pitch on a 1.8deg Motor with a 60:1 worm drive attached
#rotation_distance: 60
#microsteps: 1
#full_steps_per_rotation: 200
#gear_ratio: 60:1

# connected to Z- Endstop on S6 #2
endstop_pin: probe:z_virtual_endstop
position_max: 220 #this is set here on purpose, your actual travel will vary based on spring compression holding the bed, adjust at your own risk
position_min: -5
homing_speed: 15.0
second_homing_speed: 5.0
homing_retract_dist: 10.0
homing_positive_dir: false
 
[stepper_z1]
# connected to Y Stepper on S6 #2 (Rear Left Stepper, from top)
step_pin: s62:PD8
dir_pin: !s62:PB12
enable_pin: !s62:PD9
# Z Axis Steps per mm, uncomment out the step distance line for which motor/drive setup you are using
# SFU1204 Ballscrew attached to a 1.8 deg Motor
#rotation_distance: 16
#microsteps: 4
#full_steps_per_rotation: 200

# 20t Pulley, 3mm Pitch on a 1.8deg Motor with a 13.7:1 gearbox attached
#rotation_distance: 60
#microsteps: 4
#full_steps_per_rotation: 200
#gear_ratio: 137:10

# 20t Pulley, 3mm Pitch on a 1.8deg Motor with a 60:1 worm drive attached
#rotation_distance: 60
#microsteps: 1
#full_steps_per_rotation: 200
#gear_ratio: 60:1
 
[stepper_z2]
# connected to Z Stepper on S6 #2 (Center Right Stepper (or on belted z, Rear Right), from top)
step_pin: s62:PD14
dir_pin: !s62:PD13
enable_pin: !s62:PD15
# Z Axis Steps per mm, uncomment out the step distance line for which motor/drive setup you are using
# SFU1204 Ballscrew attached to a 1.8 deg Motor
#rotation_distance: 16
#microsteps: 4
#full_steps_per_rotation: 200

# 20t Pulley, 3mm Pitch on a 1.8deg Motor with a 13.7:1 gearbox attached
#rotation_distance: 60
#microsteps: 4
#full_steps_per_rotation: 200
#gear_ratio: 137:10

# 20t Pulley, 3mm Pitch on a 1.8deg Motor with a 60:1 worm drive attached
#rotation_distance: 60
#microsteps: 1
#full_steps_per_rotation: 200
#gear_ratio: 60:1

# [stepper_z3]
# # connected to E0 Stepper on S6 #2 (Front Right Stepper (Belted Z Only), from top) - uncomment block if needed
# step_pin: s62:PD5
# dir_pin: !s62:PD6
# enable_pin: !s62:PD4
# Z Axis Steps per mm, uncomment out the step distance line for which motor/drive setup you are using
# SFU1204 Ballscrew attached to a 1.8 deg Motor
#rotation_distance: 16
#microsteps: 4
#full_steps_per_rotation: 200

# 20t Pulley, 3mm Pitch on a 1.8deg Motor with a 13.7:1 gearbox attached
#rotation_distance: 60
#microsteps: 4
#full_steps_per_rotation: 200
#gear_ratio: 137:10

# 20t Pulley, 3mm Pitch on a 1.8deg Motor with a 60:1 worm drive attached
#rotation_distance: 60
#microsteps: 1
#full_steps_per_rotation: 200
#gear_ratio: 60:1

# TMC Stepper Configurations for All Motors
[tmc2209 stepper_x]
# connected to X Stepper on S6 #1
uart_pin: PE8
tx_pin: PE9
interpolate: false
run_current: 0.8 
sense_resistor: 0.110
stealthchop_threshold: 0
# Place a jumper on the two pin header near the endstop for sensorless homing
diag_pin: PB14 #connected to X- Endstop (X Jumper Header)
driver_SGTHRS: 115

[tmc2209 stepper_x1]
# connected to Y Stepper on S6 #1
uart_pin: PE13
tx_pin: PE14
interpolate: false
run_current: 0.8 
sense_resistor: 0.110
stealthchop_threshold: 0
# Place a jumper on the two pin header near the endstop for sensorless homing
diag_pin: PB13 #connected to Y- Endstop (Y Jumper Header)
driver_SGTHRS: 115
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

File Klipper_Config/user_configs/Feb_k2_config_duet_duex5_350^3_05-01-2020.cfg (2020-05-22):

# This file has been created by "Volcom" for the K2 Printer running a Duet Wifi Board with a Duex5
# Please change settings for your specific build or ensure you place your items in the same spots on the same MCU as I have.
# I've added as many options as I can think of for different displays as well as listed the available commands you can use via the terminal at the bottom of this configuration file.

#How do I upgrade to the latest software?
#The general way to upgrade is to ssh into the Raspberry Pi and run:
#cd ~/klipper
#git pull
#~/klipper/scripts/install-octopi.sh

#Then one can recompile and flash the micro-controller code. For example:
#make menuconfig
#make clean
#make
#sudo service klipper stop
#make flash FLASH_DEVICE=/dev/serial/by-id/ttyUSB0 (insert ID at end)
#sudo service klipper start

#However, it's often the case that only the host software changes. In this case, one can update and restart just the host software with:
#cd ~/klipper
#git pull
#sudo service klipper restart
#If after using this shortcut the software warns about needing to reflash the micro-controller or some other unusual error occurs, then follow the full upgrade steps outlined above. Note that the RESTART and FIRMWARE_RESTART g-code commands do not load new software - the above "sudo service klipper restart" and "make flash" commands are needed for a software change to take effect.

################################################################
#
# Duet specific install notes:
# Required hardware:
#
# - DuetWifi/DuetEthernet + likely a Duex board
# - Raspberry Pi 3 or higher
# - microUSB cable
#
# In it's current state, aMpeX's Duet port for Klipper requires a USB to serial adapter connected to the Duet's PanelDue connection.
# This may go away in the future but for now is still needed.
# 
# 1) Follow the standard Klipper install instructions (see: https://github.com/KevinOConnor/klipper/blob/master/docs/Installation.md)
#    During setup choose "SAM4e8e (Duet Wifi/Eth)" for the architecture and keep the default baud rate of 250000.
#    Stop after the "make menuconfig" step. Make sure the USB option is selected when making the file, not serial.
# 
# 2) To flash for your duet, connect the microUSB cable from your Pi to your Duet. 
#     - Hold the "ERASE" button on the Duet board for two seconds followed by "RESET".
#	  - obtain definition by "ls -l /dev/serial/by-id/" then unplug to verify
#     - You should now be able to successfully run the flashing step:
#	 > make menuconfig
#	 > make clean
#	 > make
#	 > sudo service klipper stop
#	 > make flash FLASH_DEVICE=/dev/serial/by-id/usb-Klipper_sam4e8e_003136535353484E3032303337303634-if00
#	 > sudo service klipper start
#
# 3) Continue the Klipper install guide at step "Configuring OctoPrint to use Klipper"
# 4) Instead of using the "~/klipper/config/example.cfg" config in the guide, use this file instead.
# 5) Run "ls -l /dev/serial/by-id/" to find the ID of the USB device. Find it and update the value in this file's [mcu] section for "serial".
# 6) In Octoprint go to the Terminal and execute command "RESTART" followed by "STATUS". Either it will report that Klipper is ready or that you have problems to fix.
#
################################################################

# use the following modifiers before the pin definition (ex: ^!ar99)
# ! 			invert the logic
# ^ 			activate 5v pullup (does not apply to all pins)
# mcu_name: 	use pins on additional MCU (ex: z:ar10)


# MCU - Duet2 + Duex5
[mcu]
#	obtain definition by "ls -l /dev/serial/by-id/" then unplug to verify
serial: /dev/serial/by-id/usb-Klipper_sam4e8e_003136535353484E3032303337303634-if00
restart_method: command

# MCU - SKR1.3
[mcu skr]
#	obtain definition by "ls -l /dev/serial/by-id/" then unplug to verify
serial: /dev/serial/by-id/usb-Klipper_lpc1768_1E50000CC0003AAFDBFB205CC02000F5-if00
restart_method: command

#virtual sdcard settings
#[virtual_sdcard]
#path: ~/.octoprint/uploads/

# Steppers
[stepper_x]
# connected to X Stepper on Duet
step_pin: PD6
dir_pin: PD11
enable_pin: !PC6
# 0.9deg - 200 steps per mm - 1/16 microstepping
step_distance: 0.005
# connected to Endstop Input X on Duet
endstop_pin: ^PC14
position_min: 0
position_endstop: 360
position_max: 360
homing_speed: 100.0
second_homing_speed: 3.0
homing_retract_dist: 3.0
homing_positive_dir: true
 
[tmc2660 stepper_x]
cs_pin: PD14
spi_bus: usart1
microsteps: 16
interpolate: True
run_current: 0.7
sense_resistor: 0.051
 
[stepper_x1]
# connected to Y Stepper on Duet
step_pin: PD7
dir_pin: !PD12
enable_pin: !PC6
# 0.9deg - 200 steps per mm - 1/16 microstepping
step_distance: 0.005

[tmc2660 stepper_x1]
cs_pin: PC9
spi_bus: usart1
microsteps: 16
interpolate: True
run_current: 0.7
sense_resistor: 0.051
 

[stepper_y]
# connected to E0 Stepper on Duet
step_pin: PD5
dir_pin: PA1
enable_pin: !PC6
# 0.9deg - 200 steps per mm - 1/16 microstepping
step_distance: 0.005
# connected to Endstop Input Y on Duet
endstop_pin: ^PA2
position_min: 0
position_endstop: 0
position_max: 360
homing_speed: 100.0
second_homing_speed: 3.0
homing_retract_dist: 3.0
homing_positive_dir: false

[tmc2660 stepper_y]
cs_pin: PC17
spi_bus: usart1
microsteps: 16
interpolate: True
run_current: 0.7
sense_resistor: 0.051

[stepper_y1]
# connected to E1 Stepper on Duet
step_pin: PD4
dir_pin: !PD9
enable_pin: !PC6
# 0.9deg - 200 steps per mm - 1/16 microstepping
step_distance: 0.005


[tmc2660 stepper_y1]
cs_pin: PC25
spi_bus: usart1
microsteps: 16
interpolate: True
run_current: 0.7
sense_resistor: 0.051



[stepper_z]
# connected to E2 Stepper on Duex(Front Left Stepper, from top)
step_pin: PD2
dir_pin: !PD28
enable_pin: !PC6
# 1.8deg - 800 steps per mm - 1/16 microstepping
step_distance: 0.00125
# connected to Z Endstop on Duet
endstop_pin: PD29

# offset for nozzle to bed off z switch
position_endstop: 2.430	#microswitch Height (further from 0 = closer to bed)
position_max: 300
position_min: -5
homing_speed: 10.0
second_homing_speed: 3.0
homing_retract_dist: 10.0
homing_positive_dir: false
 
[tmc2660 stepper_z]
cs_pin: PD23
spi_bus: usart1
microsteps: 16
interpolate: False
run_current: 0.7
sense_resistor: 0.051
 
[stepper_z1]
# connected to E3 Stepper on Duex (Rear Left Stepper, from top)
step_pin: PD1
dir_pin: !PD22
enable_pin: !PC6
# 1.8deg - 800 steps per mm - 1/16 microstepping
step_distance: 0.00125
 
[tmc2660 stepper_z1]
cs_pin: PD24
spi_bus: usart1
microsteps: 16
interpolate: False
run_current: 0.7
sense_resistor: 0.051
 
[stepper_z2]
# connected to E4 Stepper on Duex (Center Right Stepper, from top)
step_pin: PD0
dir_pin: !PD16
enable_pin: !PC6
# 1.8deg - 800 steps per mm - 1/16 microstepping
step_distance: 0.00125

[tmc2660 stepper_z2]
cs_pin: PD25
spi_bus: usart1
microsteps: 16
interpolate: False
run_current: 0.7
sense_resistor: 0.051
 


[sx1509 duex]
i2c_address: 62 #fixed on duex boards

[static_digital_output onboard_led]
pins: !PC2

# Force Move
#	used to force a single stepper to move.  not used once setup
[force_move]
enable_force_move: true

# Enable Pause/Resume Functionality
[pause_resume]

# Filament Switch Sensor.  
#	support for filament insert and runout detection using a switch sensor, such as an endstop switch.
[filament_switch_sensor my_sensor]
pause_on_runout: True
runout_gcode:
	M117 Runout Detected
	M600
	M400
event_delay: 3.0
pause_delay: 0.5
# connected to E1 Endstop on Duet
switch_pin: !PC16


# Probe
[probe]
# connected to E0 Endstop on Duet
pin: ^PD10
x_offset: 21.3 # offset for inductive probe x direction off nozzle
y_offset: 21.3 # offset for inductive probe y direction off nozzle
z_offset: 9.00 # offset for inductive probe in z height
samples: 3
sample_retract_dist: 5.0
samples_result: average
samples_tolerance: 0.050
samples_tolerance_retries: 3
speed: 15
lift_speed: 20
activate_gcode:
deactivate_gcode:

# Safe Z Home
# this allows you to home only z when the XY is already homed
[safe_z_home]
home_xy_position: 357.5,32
speed: 200.00
z_hop: 15.0
z_hop_speed: 15.0
move_to_previous: False

# Extruder0
[extruder]
# conected to Z Stepper on Duet
step_pin: PD8
dir_pin: !PD13 #inverted for BMG
enable_pin: !PC6
# LDO 0.9deg - 830 steps per mm - 1/16 microstepping -  BMG
step_distance: 0.00120481927


#0.4mm Nozzle
nozzle_diameter: 0.600
pressure_advance: 0.03
pressure_advance_smooth_time: 0.04
filament_diameter: 1.750	
max_extrude_only_distance: 1400.0
max_extrude_only_velocity: 120.0
max_extrude_only_accel: 15000.0
max_extrude_cross_section: 20000.0

# connected to Heater0 on Duet
heater_pin: !PA20
max_power: 1.0

# connected to Thermistor0 on Duet
sensor_type: EPCOS 100K B57560G104F
sensor_pin: PC15
smooth_time: 3.0

#0.4mm Nozzle Settings
smooth_time: 3.0
max_power: 1.0
control: pid
pid_Kp: 27.995
pid_Ki: 1.403
pid_Kd: 139.625
min_extrude_temp: 0
min_temp: 0
max_temp: 300

[verify_heater extruder]
hysteresis: 10
check_gain_time: 40
heating_gain: 2
max_error: 500
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

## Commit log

2020-03-04 add STLs, dxfs, print settings, and bed drawing for k2 R1A1
    add STLs, dxfs, print settings, and bed drawing for k2 R1A1
    [Back_Panel_200mm_x_200mm_Rev1.DXF, Back_Panel_250mm_x_250mm_Rev1.DXF, Back_Panel_300mm_x_300mm_Rev1.DXF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]
2020-03-04 gain missing 25mm in Y direction
    [Gantry_Deck_Panel_200mm_x_200mm_Rev1.DXF, Gantry_Deck_Panel_250mm_x_250mm_Rev1.DXF, Gantry_Deck_Panel_300mm_x_300mm_Rev1.DXF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]
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2020-03-11 bolt in too from the underside, no more requirement to remove extruder to swap tool
    [xy_carriage_top_plate_x1_rev2.STL, xy_carriage_top_plate_x1_rev3.STL, xy_carriage_v6_tool_mount_1_x1_rev1.STL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]
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2020-03-19 add emergency bed/gantry overtravel stops to prevent mechanical damage in the event of a nozzle crash
    [z_overtravel_e_stop_x4_rev1.STL]
2020-03-24 add initial revision of BMG support to toolhead
    add initial revision of BMG support to toolhead
    [[a]_duet3_toolboard_holder_x1_rev1.STL, [a]_duet3_toolboard_holder_x1_rev2.STL, [a]_xy_carriage_fan_duct_1_x1_rev3.STL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]
2020-03-25 add UHP-350 bracket, fix interference in electrical box corner, remove tolerance stackup in electrical panel cover
    add UHP-350 bracket, fix interference in electrical box corner, remove tolerance stackup in electrical panel cover
    [Back_Panel_350mm_x_390mm_Rev2.DXF, Side_Screw_Panel_350mm_x_390mm_Rev1.DXF, [a]_electronics_box_corner_x4_rev1.STL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]
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2020-03-28 update bed design, reduce twist, increase stiffness
    update bed design, reduce twist, increase stiffness
    [magnetic_probe_dock_x1_rev1.STL, magnetic_probe_dock_x1_rev2.STL, z_gantry_to_shoulder_bolt_bar_x3_rev1.STL]
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2020-03-29 xy tower had m5 clearance hole, should have been m4 clearance hole
    [[a]_bearing_cap_x4_rev2.STL, [a]_bearing_cap_x4_rev3.STL, short_motor_tall_idler_mount_x2_rev4.STL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]
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2020-03-29 thicken walls of part cooling ducts, add flange to aid in printing
    [[a]_xy_carriage_fan_duct_1_x1_rev4.STL, [a]_xy_carriage_fan_duct_1_x1_rev5.STL, [a]_xy_carriage_fan_duct_2_x1_rev4.stl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]
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2020-03-31 remote sharp point from part cooling duct, printability
    remote sharp point from part cooling duct, printability
    [[a]_xy_carriage_fan_duct_1_x1_rev5.STL, [a]_xy_carriage_fan_duct_1_x1_rev6.STL, [a]_xy_carriage_fan_duct_2_x1_rev5.stl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]
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2020-04-02 tighten xy rail block, new z tower to more easily replace and remove nema17 motor
    [xy_rail_holder_x4_rev1.STL, xy_rail_holder_x4_rev2.STL, z_motor_spacer_NEMA17_1_x3_rev1.STL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]
2020-04-02 extend nema17 main body by 4mm, too short. Fix wrong configuration xy rail holder
    extend nema17 main body by 4mm, too short. Fix wrong configuration xy rail holder
    [xy_rail_holder_x4_rev2.STL, z_motor_spacer_NEMA17_1_x3_rev1.STL, z_motor_spacer_NEMA17_1_x3_rev2.STL]
2020-04-03 new, more user service-able motor towers for XY axis
    new, more user service-able motor towers for XY axis
    [[a]_bearing_cap_x4_rev3.STL, [a]_bearing_cap_x4_rev4.STL, short_motor_tall_idler_mount_1_x2_rev1.STL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]
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2020-04-04 enlarge clearance holes on motor plate to motor base screws
    [motor_idler_top_plate_x4_rev1.STL, short_motor_tall_idler_mount_2_x2_rev1.STL, short_motor_tall_idler_mount_x2_rev2.STL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]
2020-04-04 add sharp corner clearance to xy rail holder, stress relief
    add sharp corner clearance to xy rail holder, stress relief
    [xy_rail_holder_x4_rev2.STL, xy_rail_holder_x4_rev3.STL]
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2020-04-09 shorten grommet stickout, hard to route wires cleanly otherwise
    [wiring_grommet_screw_left_25mm_x2_rev1.STL, wiring_grommet_screw_left_25mm_x2_rev2.STL, wiring_grommet_screw_left_35mm_x1_rev2.STL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]
2020-04-10 lighten/refactor mosquito mount
    supports 30 and 40mm fan with adapter, hotend rotated 90deg
    [xy_carriage_mosquito_tool_mount_x1_rev2.STL, xy_carriage_mosquito_tool_mount_x1_rev3.STL]
2020-04-11 move power inlet closer to corner of box (easier to route wiring to PSU)
    [electronics_box_side_panel_TE_power_inlet_x1_rev2.DXF]
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2020-04-12 refactor xy carriage, add lightness and air
    refactor xy carriage, add lightness and air
    [[a]_xy_carriage_fan_duct_1_x1_rev6.STL, [a]_xy_carriage_fan_duct_1_x1_rev7.STL, [a]_xy_carriage_fan_duct_2_x1_rev6.stl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]
2020-04-14 remove duet toolboard mount, tweak length and clearance on cable anchor on x carriage, add magnet removal holes to probe pickup
    [[a]_duet3_toolboard_holder_x1_rev2.STL, xy_carriage_cable_anchor_x1_rev1.STL, xy_carriage_cable_anchor_x1_rev2.STL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]
2020-04-15 z_tilt typo, fix
    [K2_bigtree_skr_1.3_config-250mm_x_250mm_x_250mm_build.cfg]
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2020-04-16 correct minor dimensional typo in deck plates
    [Gantry_Deck_Panel_200mm_x_200mm_Rev4.DXF, Gantry_Deck_Panel_250mm_x_250mm_Rev4.DXF, Gantry_Deck_Panel_300mm_x_300mm_Rev4.DXF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]
2020-04-16 stiffen bmg mounting bracket
    [bmg_mounting_bracket_x1_rev1.STL, bmg_mounting_bracket_x1_rev2.STL]
2020-04-18 fix non-manifold parts
    fix non-manifold parts
    [[a]_xy_carriage_fan_duct_2_x1_rev7.stl]
2020-04-19 dual xy switch drive tower support
    dual xy switch drive tower support
    [[a]_bearing_cap_x4_rev4.STL, [a]_bearing_cap_x4_rev5.STL, short_motor_tall_idler_mount_x2_rev2.STL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]
2020-04-19 xy tower idlers use same bolt length for all 4 bolts, update edrawing
    xy tower idlers use same bolt length for all 4 bolts, update edrawing
    [[a]_bearing_cap_x4_rev5.STL, [a]_short_motor_tall_idler_bearing_cap_x2_rev1.STL, [a]_tall_motor_short_idler_bearing_cap_x2_rev1.STL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]
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2020-04-22 z ballscrew+rail block from heatset inserts to thru bolts and nylon lock nuts
    [z_bearing_block_b_mirror_x2_rev2.STL, z_bearing_block_b_mirror_x2_rev3.STL, z_bearing_block_b_x1_rev2.stl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]
2020-04-22 replace z rail alignment tool with correct one, tighten tolerances on rail alignment tools
    replace z rail alignment tool with correct one, tighten tolerances on rail alignment tools
    [[a]_mgn9_3rd_z_rail_install_tool_x3_rev1.stl, [a]_mgn9_3rd_z_rail_install_tool_x3_rev2.stl, [a]_mgn9_rail_install_tool_2060_x3_rev1.STL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]
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2020-04-25 add experimental 16t drive/idler pulley support
    add experimental 16t drive/idler pulley support
    [xy_tensioner_left_16t_drive_x4_rev1.STL, xy_tensioner_left_20t_drive_x4_rev2.STL, xy_tensioner_right_16t_drive_x4_rev1.STL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]
2020-04-27 M4 heatset inserts were too tight on install, short tower M3 screw clearance hole for motor to base was too small (3.3 vs 3.6)
    M4 heatset inserts were too tight on install, short tower M3 screw clearance hole for motor to base was too small (3.3 vs 3.6)
    [motor_idler_top_plate_x4_rev1.STL, short_motor_tall_idler_mount_x2_rev4.STL, short_motor_tall_idler_mount_x2_rev5.STL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]
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2020-05-06 z chain anchors were missing from stl folder
    [[a]_bed_wiring_retaining_clip_x2_rev1.STL, bed_wiring_retaining_clip_x2_rev1.STL, z_chain_anchor_bottom_x1_rev1.STL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]
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2020-05-31 update xy carriage top plate to restore full xy travel, stiffen part by 15%
    [bmg_xy_carriage_top_plate_x1_rev2.STL, bmg_xy_carriage_top_plate_x1_rev3.STL]
2020-06-03 add optional laser cut top and bottom panels
    add optional laser cut top and bottom panels
    [Bottom_200mm_x_200mm_Rev1.DXF, Bottom_250mm_x_250mm_Rev1.DXF, Bottom_300mm_x_300mm_Rev1.DXF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]
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2020-07-05 idler tower beefup, update edrawings
    fix extremely rare case where the xy idler top cap can split (aka 12k accel at 500mm/s for extended periods of time), by reducing stress points present and increasing radius sizes in weaker regions.
    [[a]_short_motor_tall_idler_bearing_cap_x2_rev1.STL, [a]_short_motor_tall_idler_bearing_cap_x2_rev2.STL, [a]_tall_motor_short_idler_bearing_cap_x2_rev1.STL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]
2020-07-07 add reinforcing ribs to bmg top plate
    trying to stiffen tool mounting point in an effort to reduce low speed ringing
    [bmg_xy_carriage_top_plate_x1_rev3.STL, bmg_xy_carriage_top_plate_x1_rev4.STL]
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2020-07-28 add printed BF10 (bottom bearing) replacement block
    optional for now, requires 608 bearing
    [printed_BF10_block_alternative_x3_rev1.STL]
2020-07-28 fix stl orientation
    [printed_BF10_block_alternative_x3_rev1.STL]
2020-07-28 add high flow variant of ducting (for pla, etc)
    add high flow variant of ducting (for pla, etc)
    [[a]_xy_carriage_fan_duct_1_high_flow_x1_rev1.STL, [a]_xy_carriage_fan_duct_2_high_flow_x1_rev1.STL]
2020-07-29 revision 2 of high flow fan ducting
    revision 2 of high flow fan ducting
    [[a]_xy_carriage_fan_duct_1_high_flow_x1_rev1.STL, [a]_xy_carriage_fan_duct_1_high_flow_x1_rev2.STL, [a]_xy_carriage_fan_duct_2_high_flow_x1_rev1.STL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]
2020-07-29 Revert "revision 2 of high flow fan ducting"
    This reverts commit 5c57c56358eb46985ad022c85fca6f6c0acb7b73.
    [[a]_xy_carriage_fan_duct_1_high_flow_x1_rev1.STL, [a]_xy_carriage_fan_duct_1_high_flow_x1_rev2.STL, [a]_xy_carriage_fan_duct_2_high_flow_x1_rev1.STL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]
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2020-07-31 add oldham coupler style joint to z axis
    reduces chances of bent screws (especially if your on a budget) of affecting print quality
    [z_bearing_block_a_mirror_oldham_x1_rev1.STL, z_bearing_block_a_oldham_x2_rev1.STL, z_bearing_block_a_x3_rev2.STL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]
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2020-08-04 high flow fan duct now standard
    high flow fan duct now standard
    [[a]_xy_carriage_fan_duct_1_high_flow_x1_rev1.STL, [a]_xy_carriage_fan_duct_1_high_flow_x1_rev2.STL, [a]_xy_carriage_fan_duct_1_x1_rev8.STL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]
2020-08-04 reduce material usage on probe dock
    reduce material usage on probe dock
    [magnetic_probe_dock_x1_rev3.STL, magnetic_probe_dock_x1_rev4.STL]
2020-08-06 oldham pockets werent set on layer multiples, move idler tower on xy 1mm forward for more motor clearance
    oldham pockets werent set on layer multiples, move idler tower on xy 1mm forward for more motor clearance
    [short_motor_tall_idler_mount_x2_rev6.STL, short_motor_tall_idler_mount_x2_rev7.STL, tall_motor_short_idler_mount_x2_rev6.STL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]
2020-08-06 minor oldham slot geometry adjustment for better printability
    minor oldham slot geometry adjustment for better printability
    [z_bearing_block_a_mirror_oldham_x1_rev2.STL, z_bearing_block_a_mirror_oldham_x1_rev3.STL, z_bearing_block_a_oldham_x2_rev2.STL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]
2020-08-06 prevent flat sections from appearing in oldham pockets
    prevent flat sections from appearing in oldham pockets
    [z_bearing_block_a_mirror_oldham_x1_rev3.STL, z_bearing_block_a_mirror_oldham_x1_rev4.STL, z_bearing_block_a_oldham_x2_rev3.STL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]
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2020-08-08 quantity on mirror and std was inverted
    quantity on mirror and std was inverted
    [z_bearing_block_a_mirror_oldham_x2_rev4.STL, z_bearing_block_a_oldham_x1_rev4.STL]
2020-08-13 add Meanwell LRS-200 and LRS-350 (and RSP) mounting bracket for converts from other machines
    add Meanwell LRS-200 and LRS-350 (and RSP) mounting bracket for converts from other machines
    [meanwell_lrs_200&350_24_psu_mounting_bracket_x2_rev1.STL]
2020-08-13 add sensorless homing, input shaper and bmg direct drive support to config
    [K2_bigtree_skr_1.3_config-250mm_x_250mm_x_250mm_build.cfg]
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2020-08-16 hollow out electronics box corner, reduce material and print time
    hollow out electronics box corner, reduce material and print time
    [[a]_electronics_box_corner_x4_rev2.STL, [a]_electronics_box_corner_x4_rev3.STL]
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2020-08-26 chain anchors had holes for m3 inserts, should be m4, simplify and add lightness
    chain anchors had holes for m3 inserts, should be m4, simplify and add lightness
    [z_chain_anchor_bottom_x1_rev2.STL, z_chain_anchor_bottom_x1_rev3.STL, z_chain_anchor_top_x1_rev2.STL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]
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2020-09-03 fix print orientation on part
2020-09-07 replace normal ascender top plate with folded ascender top plate
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2020-09-15 Update README.md
    Release Schedule:
    - Release 1 - RC2: Final True Release
    - Release 1: Bug Fixes from Final Testing of RC2
    - Release 1.1: Belted Z Drive Option
    - Release 1.2: New Front Door Design
    - Release 2.0: New Gantry
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2020-10-04 fix print orientation for parts
    [xy_tensioner_left_20t_drive_x4_rev3.STL, xy_tensioner_right_20t_drive_x4_rev5.STL]
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2020-10-19 create jigs and fixtures folder, add belted z install spacer tool
    [[a]_bed_wiring_retaining_clip_x2_rev1.STL, [a]_belted_z_install_jig_x1_rev1.STL, [a]_mgn9_3rd_z_rail_install_tool_x3_rev2.stl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]
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2020-10-22 add DXFs, PDFs and wiring schematic to release 1.1, remove deck plate, remove filament switch cluster
    removed parts are not compatible with belted z
    [Back_Panel_200mm_x_200mm_Rev2.DXF, Back_Panel_250mm_x_250mm_Rev2.DXF, Back_Panel_300mm_x_300mm_Rev2.DXF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]
2020-10-23 coupler needed additional clearance on drive tower
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2020-11-18 replace 10x3 CS piton with 6x3 flat magnet piton
    [[a]_piton_probe_cap_6x3_x1_rev2.STL, [a]_piton_probe_plate_6x3_x1_rev2.STL, [a]_piton_probe_plate_x1_rev1.STL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]
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2020-11-18 add skr1.4 config, fix minor typos on 1.3 config, remove old 1.3 code
    [K2_bigtree_skr_1.4_config-250mm_x_250mm_x_250mm_build.cfg]
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2020-11-19 upload correct model of endcap
    [[a]_2040_extrusion_endcap_x2_rev1.STL, [a]_2040_extrusion_endcap_x2_rev2.STL]
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2020-11-25 fix motor key flange interference in motor mounts
2020-11-26 fix print orientation
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2020-11-27 couldnt pass SHCS thru access holes, fixed that
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2020-12-06 wrong uart/tx on z3
    [K2_fysetc_s6_1.2_config-250mm_x_250mm_x_250mm_build.cfg]
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2020-12-09 add missing stls, dxfs, and pdfs to release 2 folder
    [BF10_block_x3_rev1.STL.STL, Back_Panel_200mm_x_200mm_Rev2.DXF, Back_Panel_250mm_x_250mm_Rev2.DXF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]
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2020-12-29 add fixed probe feb configs
    [k2_config_release2xy_3beltedz_fixed-probe.cfg, k2_config_release2xy_4beltedz_fixed-probe-mental.cfg, k2_config_release2xy_ballscrewz.cfg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]
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2020-12-31 uploaded wrong toolhead
2021-01-01 5020 fan pocket clearance
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2021-01-07 bad at math, fix doors, add 450 and 500mm doors
    [Front_Door_250mm_x2_Rev2.DXF, Front_Door_300mm_x2_Rev2.DXF, Front_Door_350mm_x2_Rev2.DXF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]
2021-01-08 replace step_distance with rotation_distance on release 1.2 configs
    [K2_bigtree_skr_1.3_config-250mm_x_250mm_x_250mm_build.cfg, K2_bigtree_skr_1.4_config-250mm_x_250mm_x_250mm_build.cfg, K2_fysetc_s6_1.2_config-250mm_x_250mm_x_2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]
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2021-01-08 add microstepping and full steps per rotation sections to config, they were missed by mistake
    [K2_bigtree_skr_1.3_config-250mm_x_250mm_x_250mm_build.cfg, K2_bigtree_skr_1.4_config-250mm_x_250mm_x_250mm_build.cfg, K2_fysetc_s6_1.2_config-250mm_x_250mm_x_2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]
2021-01-08 add s6 2.0 config, fix pin issue on 1.2 config
    [K2_fysetc_s6_2.0_config-250mm_x_250mm_x_250mm_build.cfg]
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2021-01-19 add draft to probe dock and probe housing to aid in entry when dock is slightly misaligned
    [omron_d2f-5_microswitch_probe_body_x1_rev1.STL, omron_d2f-5_microswitch_probe_body_x1_rev2.STL]
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2021-01-22 dragon tool mount was 1mm too long, add 1st stage of new fan duct setup
    [[a]_xy_carriage_dragon_tool_mount_x1_rev4.STL, [a]_xy_carriage_dragon_tool_mount_x1_rev5.STL, xy_carriage_bottom_frame_magswitch_probe_v2_x1_rev3.STL]
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2021-03-03 belt retaining screw was 5.3mm insert hole, corrected to 4.7mm
    [xy_mgn12c_tensioner_left_20t_drive_12mm_belts_x4_rev1.STL, xy_mgn12c_tensioner_left_20t_drive_12mm_belts_x4_rev2.STL, xy_mgn12c_tensioner_right_20t_drive_12mm_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]
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2021-04-19 fix hole alignment in spool holder
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2021-05-05 revised toolhead for more stability at 12k+ accels, more umbilical stability
    [[a]_carabiner_mounting_bracket_x1_rev1.STL, xy_carriage_bottom_frame_magswitch_probe_v2_x1_rev3.STL]
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2021-05-25 add extremely preliminary mag+ support (requires flipping the magswitch dock 180deg in the holder to work)
    [[a]_xy_carriage_mellow_mosquito_tool_mount_x1_rev1.STL, [a]_xy_carriage_std_fan_duct_1_x1_rev1.STL, [a]_xy_carriage_std_fan_duct_2_x1_rev1.STL]
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2021-05-29 shorten stack height of rpi bracket to better fit on k3 printers
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2021-05-30 fix virtual endstop typo
    [K2_fysetc_spider_+_btt_motor_expander_config-250mm_x_250mm_x_250mm_build.cfg]
2021-05-30 bed mesh fade fix
    [K2_fysetc_s6_2.0_+_btt_motor_expander_config-250mm_x_250mm_x_250mm_build.cfg, K2_fysetc_s6_2.0_x2_config-250mm_x_250mm_x_250mm_build.cfg, K2_fysetc_spider_+_bt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]
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2021-07-12 fan mount broke sub 5 minutes, make thicker
    [[a]_xy_carriage_fan_mount_1_x1_rev3.STL, [a]_xy_carriage_fan_mount_2_x1_rev3.stl]
2021-07-18 fix hole size (now 6mm) on tall motor xy tower
    [tall_motor_short_idler_mount_12mm_belts_x2_rev4.STL]
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2021-08-30 fix missing set screw cutout in 2.1 z drive
    [[a]_40+20to1_z_drive_1_mirror_x2_rev1.STL, [a]_40+20to1_z_drive_1_x2_rev1.STL, [a]_40+20to1_z_drive_2_mirror_x2_rev1.STL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]
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2021-11-02 fix electronics brackets hole alignment
    [[a]_universal_controller_mounting_bracket_b_x2_rev1.STL, [a]_universal_rpi_mounting_bracket_b_x2_rev1.STL, universal_controller_mounting_bracket_a_x2_rev2.STL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]
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2022-01-22 fix 60:1 gear interference with metal top plate
    [3mm_stainless_belted_worm_z_metal_top_60to1_x4_rev2.DXF]
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2022-02-06 fix endstop typo
    [K2_fysetc_spider_+_btt_motor_expander_config-250mm_x_250mm_x_250mm_build.cfg]
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2022-03-02 exported wrong side panel (without brace in middle)
    [electronics_box_side_structural_panel_x4_rev1.DXF]
2022-03-07 fix motor power grommet location such that they dont collide with RHS motor
    [Back_Panel_200x200_Rev5.dxf, Back_Panel_250x250_Rev5.dxf, Back_Panel_300x300_Rev5.dxf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]
2022-03-22 fix missing fillet
    [electronics_box_blanking_plate_x2_rev1.STL, electronics_box_blanking_plate_x2_rev2.STL]
2022-04-11 Fix EXP pin aliases for Spider.
    [K2_fysetc_spider_+_btt_motor_expander_config-250mm_x_250mm_x_250mm_build.cfg]
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2022-04-29 prevent z idler position from rotating...ever
    [40+20to1_z_drive_3_mirror_x2_rev1.STL, 40+20to1_z_drive_3_x2_rev1.STL, 40+20to1_z_drive_4_x4_rev1.STL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]
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2022-05-20 fix missing comment line on force move command
    [K2_fysetc_s6_2.0_+_btt_motor_expander_config-250mm_x_250mm_x_250mm_build.cfg, K2_fysetc_s6_2.0_x2_config-250mm_x_250mm_x_250mm_build.cfg, K2_fysetc_spider_+_bt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]
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2022-12-18 more clearance for longer screw to secure magnet
    [electronics_box_corner_mains_inlet_x1_rev3.STL, electronics_box_corner_mains_inlet_x1_rev4.STL, electronics_box_corner_x3_rev2.STL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]
2023-01-13 add heatsets to toolhead, shorten fan screws
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2023-02-20 fix small mirroring error in part (cutouts)
    [toolhead_main_plate_sherpa_mini_x2_rev4_2mm_aluminum.DXF]
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2023-05-02 remove obsolete z drive to prevent confusion
    [3mm_stainless_belted_worm_z_metal_bottom_40+20to1_x4_rev2.DXF, 3mm_stainless_belted_worm_z_metal_bottom_60to1_x4_rev2.DXF, 3mm_stainless_belted_worm_z_metal_to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]
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
